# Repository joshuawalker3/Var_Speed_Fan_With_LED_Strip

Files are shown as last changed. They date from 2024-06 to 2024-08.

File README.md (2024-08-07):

# **Variable Speed Desk Fan with RGB LED for Use While Soldering**

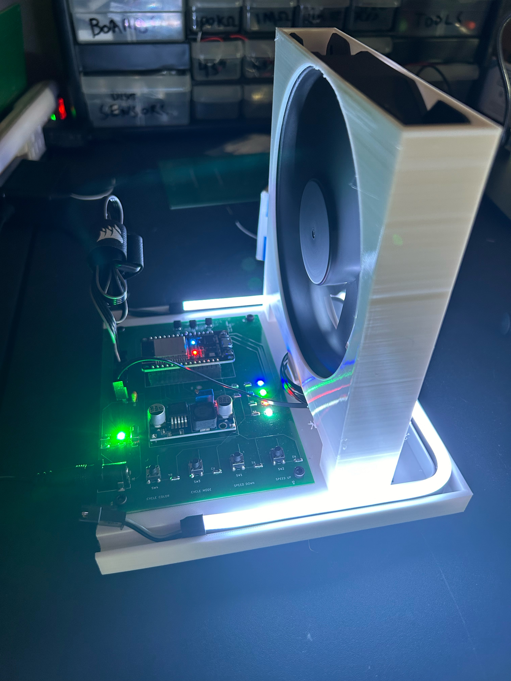
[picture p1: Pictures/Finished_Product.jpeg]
Final-Product


## **Project Overview**
An annoyance I’ve had while soldering is that the fumes from the flux burning off tends to drift directly in my face and up my nose. To solve this issue, I made this desktop fan. The fan is actually a PC chassis fan and the LED strip is a cheap LED strip. Any strip will work as long as they have a 4 pin connection and are Common Anode.

## **Code**
### *Overview*
The code is written in C. No IDE was used, only sublime text editor (because it’s the superior text editor).

Overall, the code is pretty straightforward. After initializing structs representing a motor (the fan) and the LED strip, they are used to initialize their respective functions then the drivers for each are started as their own task so they can run in “parallel”. The drivers and related functions are contained in components so the code header can be linked when the ELF is built by the toolchain.

The fan is represented in the code as a Pulse Width Modulated (PWM) DC-motor. The struct is used to set up the PWM module and the GPIO pins for controlling motor speed. A 2-bit resolution for the PWM was chosen since I only desired to have three speeds for the fan: off, half-power, and full-power. The motor driver polls the GPIO pins and, when an input is detected, changes the motor speed accordingly.

The LED strip is controlled via signals from 3 GPIO pins, 1 for each color. The LED has two modes. The static mode where a chosen color is displayed indefinitely and the cycle mode where every color combination is cycled through sequentially. The LED driver polls two input pins. The first input pin cycles through colors sequentially and can cycle power to the LED if pressed for 1 second. The second input changes the LED mode.
### *Challenges and Lessons Learned*
The biggest challenge with the code was figuring out the toolchain and how the build system works. A good chunk of time was spent trying to figure out how to integrate the header into the main code. The solution to this was obviously to RTFM. The biggest lesson learned was the value of structs. By putting all needed variables into pretty little structs, the code became easier to read as well as to write.

## **Chassis Design and Manufacture**
### *Overview*
The chassis was designed in FreeCAD, sliced using Ankermake default slicer, and printed on an Ankermake M5. It was printed as one solid piece. The chassis is simply a plastic base connected to a slot for the fan and slots for the LED strip and PCB. It was designed to be as compact as possible while maintaining stability.

#### FreeCAD Model
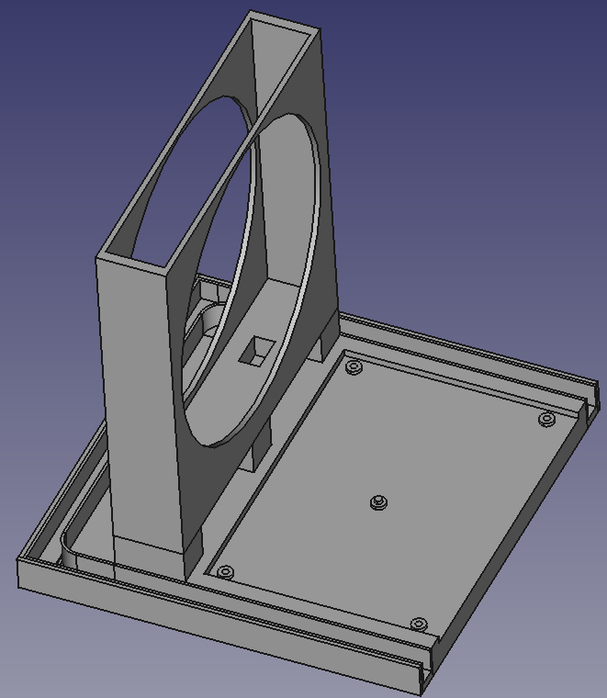
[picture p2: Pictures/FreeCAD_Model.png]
Model


### *Challenges and Lessons Learned*
The main challenge with the chassis was getting it to print properly. Since that are parts that are “floating” while the print is in process, supports were required for the fan slot and the circular vertical hole. The print failed twice for what is suspected to be the same reason. The solution was to simply to slow the speeds down across the board for the entire print. This caused the print time to inflate from around 11 hours to 30 hours.
#### Failed Print
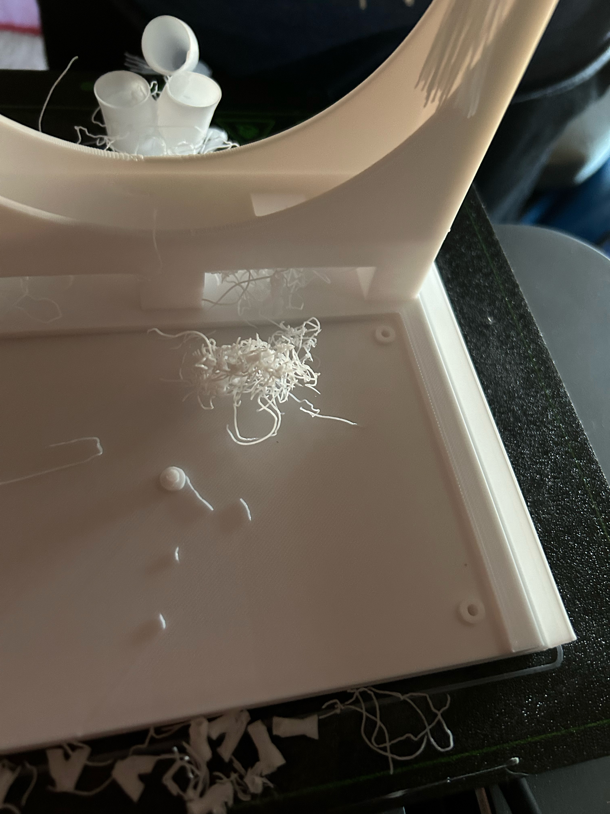
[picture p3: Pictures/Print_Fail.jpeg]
Print-Fail


#### Proper Print with Supports Connected
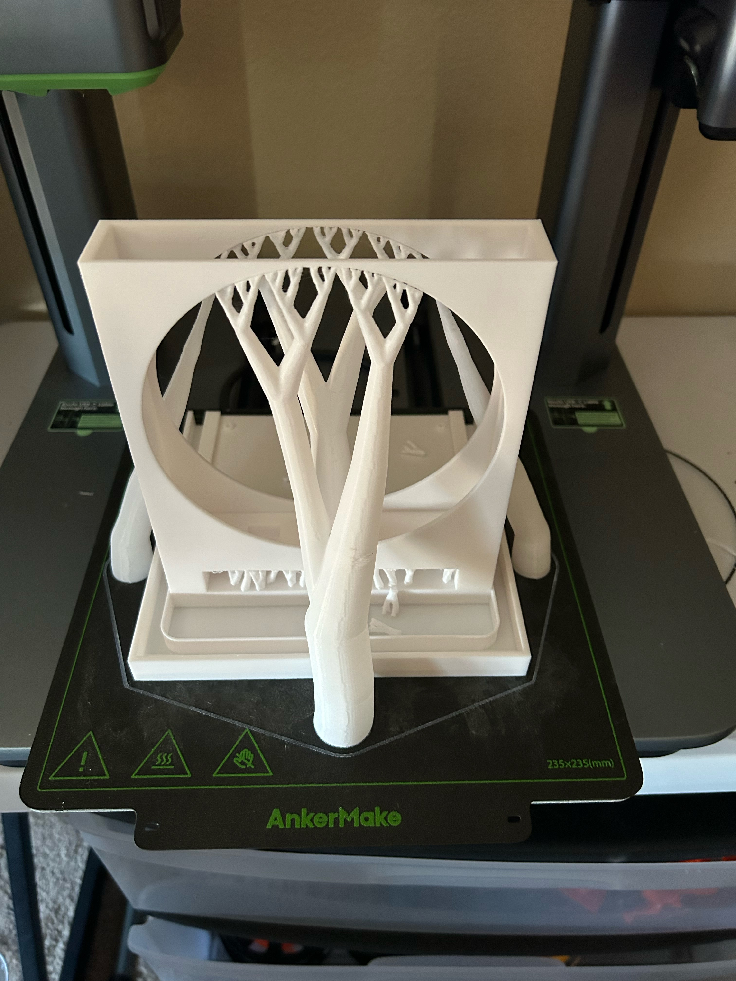
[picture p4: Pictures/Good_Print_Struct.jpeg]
Good-Print


#### Final Print
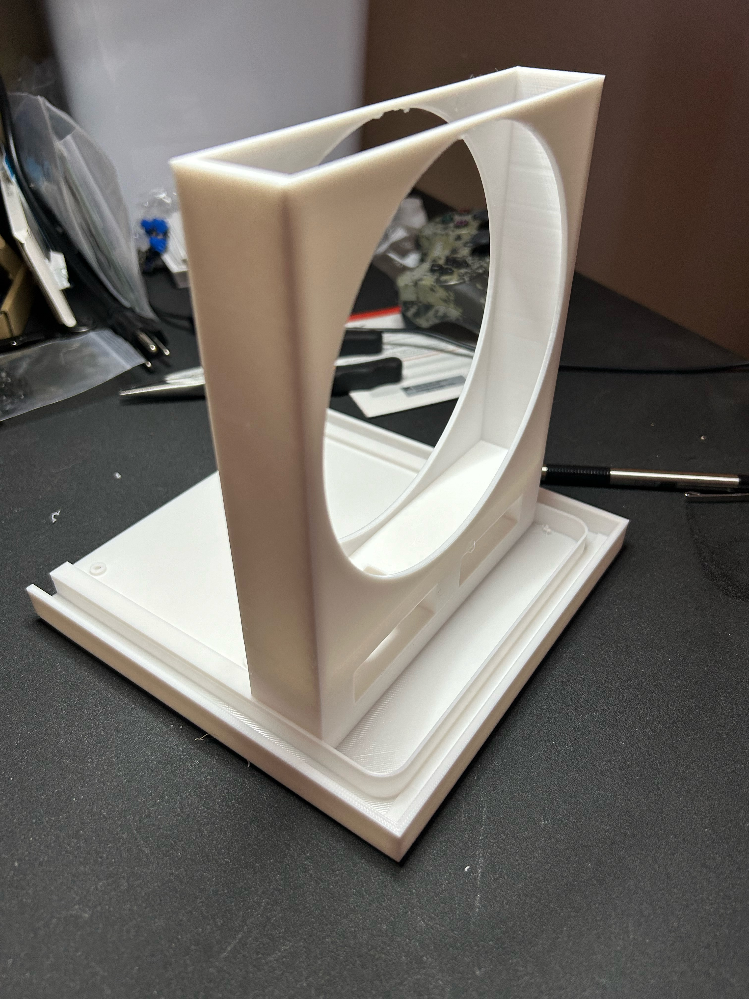
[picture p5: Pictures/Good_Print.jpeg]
Final-print


## **PCB Design**
### *Overview*
The PCB was designed using KiCAD and manufactured through PCBWay. I changed PCB manufacturers out of curiousity but could find no signifigance between PCBWay and Seeed Fusion.

Since the fan and LED strip require 12 VDC and the ESP32 requires between 3.3 – 6 VDC, the circuit is split by a buck converter that transforms 12VDC to8 around 5 VDC (I used 4.5 VDC). The PWM signal is sent directly from the ESP board to the fan. The LED strip interfaces to the ESP board via PN-2222A transistors.

#### PCB Schematic
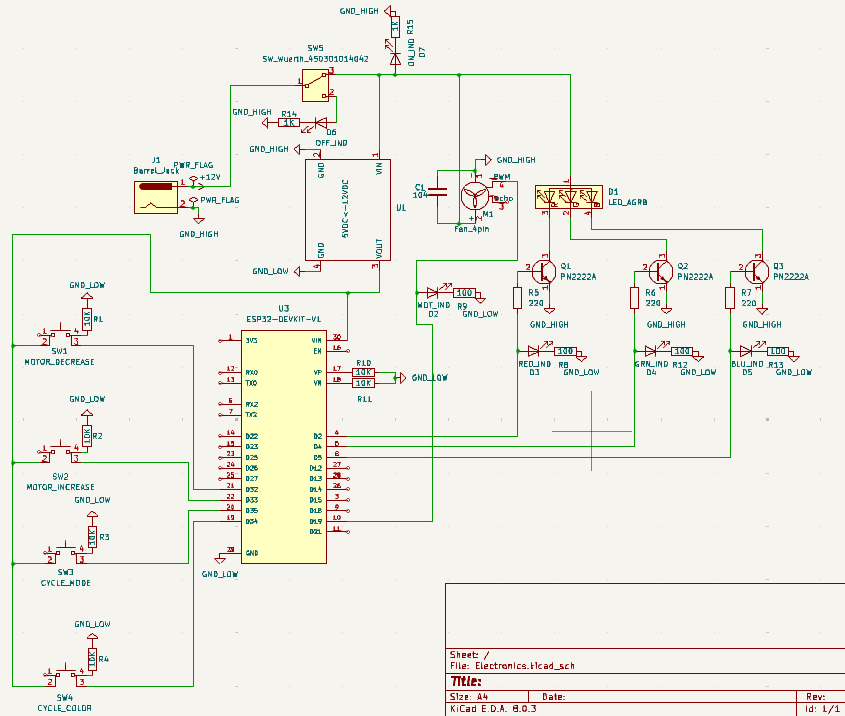
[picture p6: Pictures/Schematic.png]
Schematic


#### Circuit Prototype
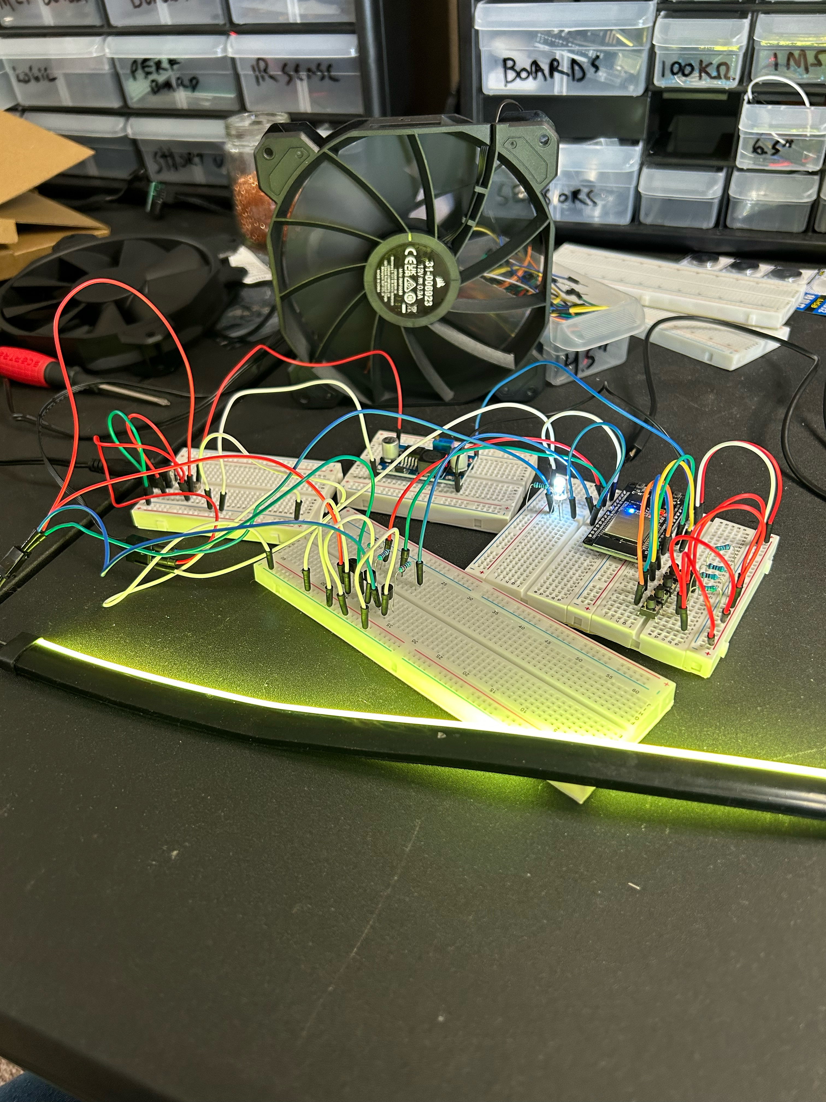
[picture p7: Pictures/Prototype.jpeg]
Prototype


#### PCB Design
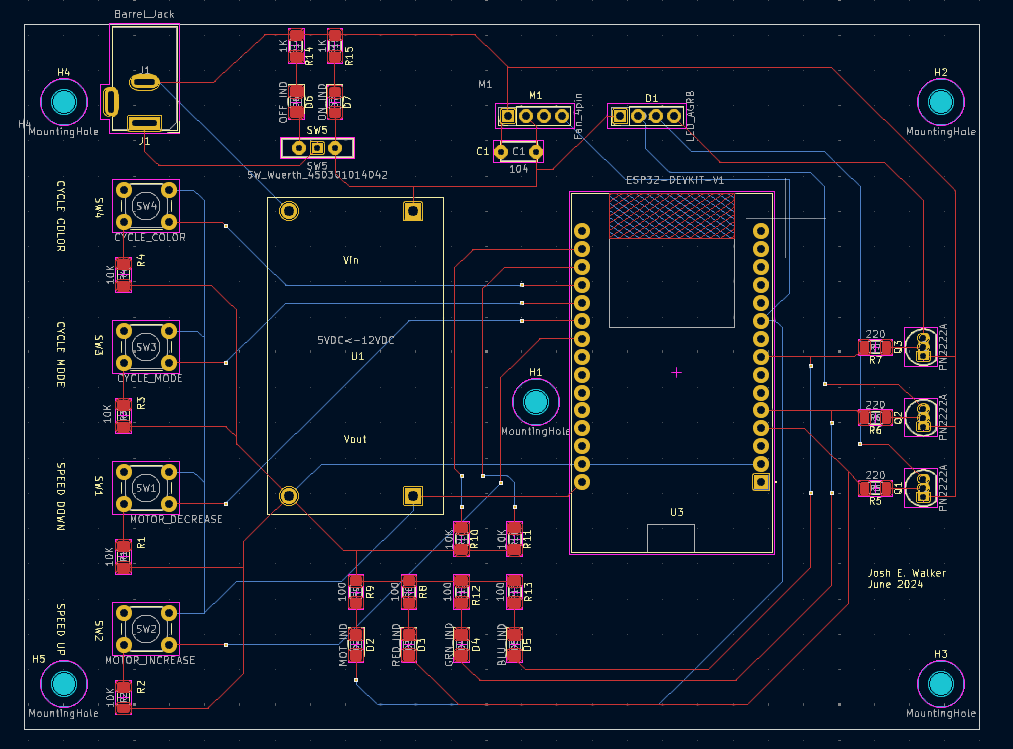
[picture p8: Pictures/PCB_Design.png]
PCB-Design


I also added some components to aid in troubleshooting such as LED’s that indicate that power is being applied to the board when off, an indication the model is on, LED’s connected in parallel to each LED GPIO to show proper response, and an LED in parallel to the fan that shows the status of the fan since the LED will change brightness as the PWM signal, and therefore fan speed, changes.
### *Challenges and Lessons Learned*
This was a big step for me in PCB design since it had more components than I had ever used before. This meant that I had to be creative with routing traces. To further remove trace clutter on the PCB, I added via’s so I could have traces on both the top and bottom of the PCB.

#### PCB Comparison Before and After Soldering Components
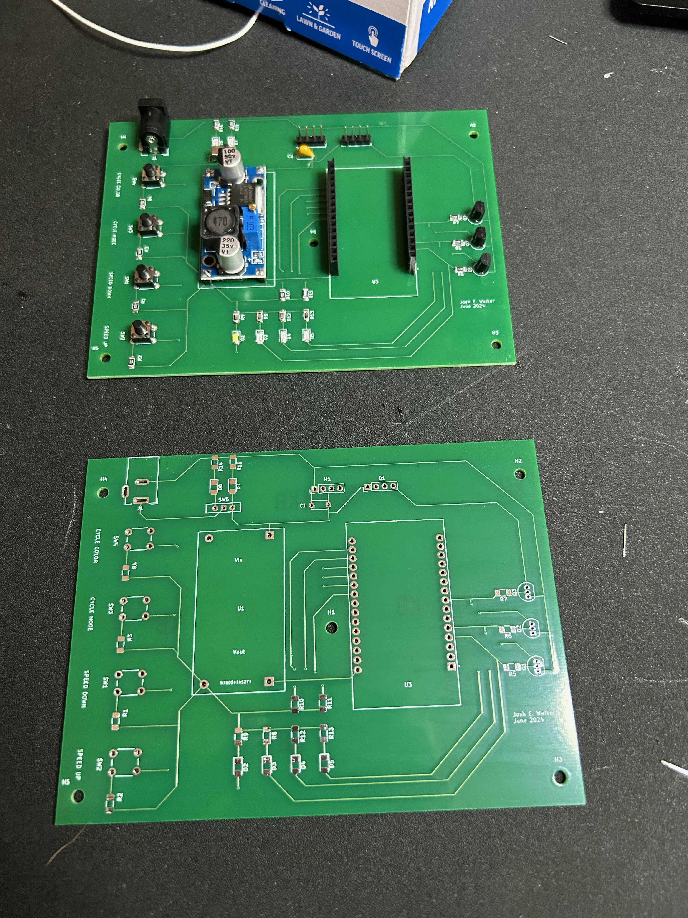
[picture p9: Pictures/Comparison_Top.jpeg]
Top

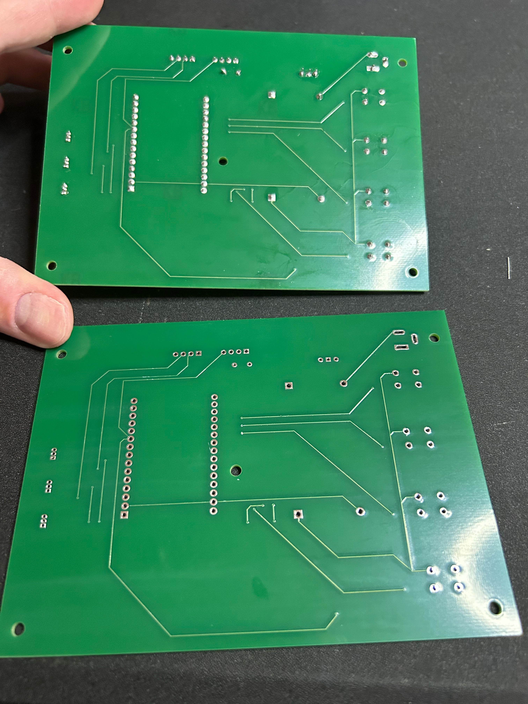
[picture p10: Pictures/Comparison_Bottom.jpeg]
Bottom


#### PCB Mounted on Chassis
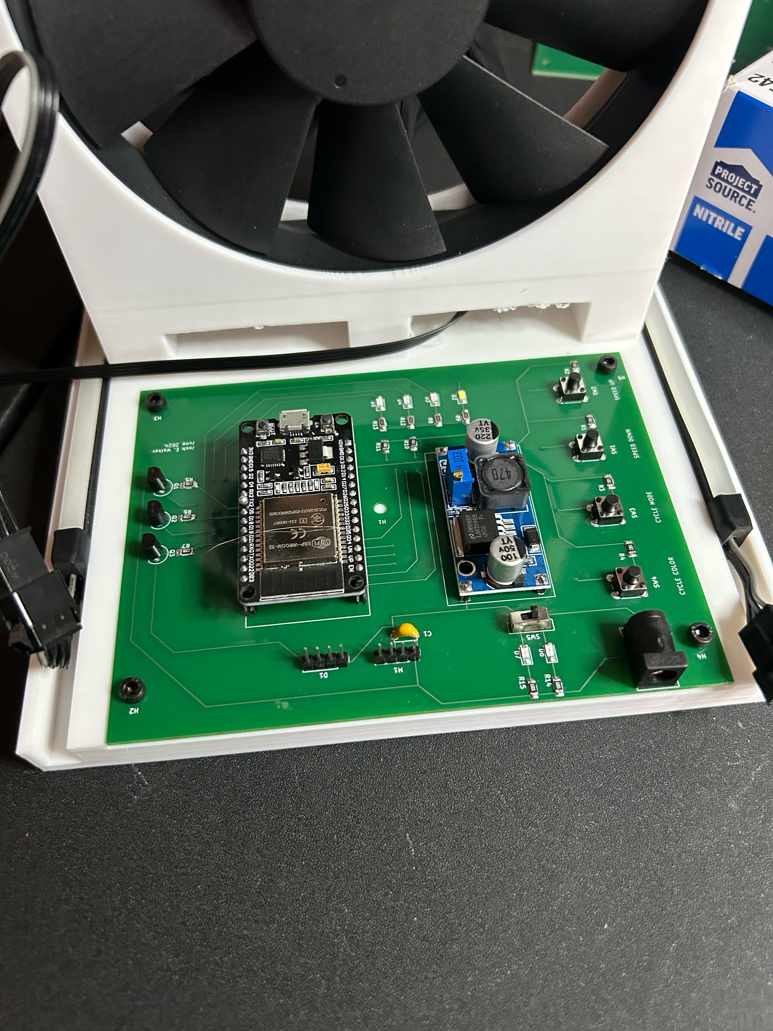
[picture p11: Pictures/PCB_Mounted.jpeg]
Mounted


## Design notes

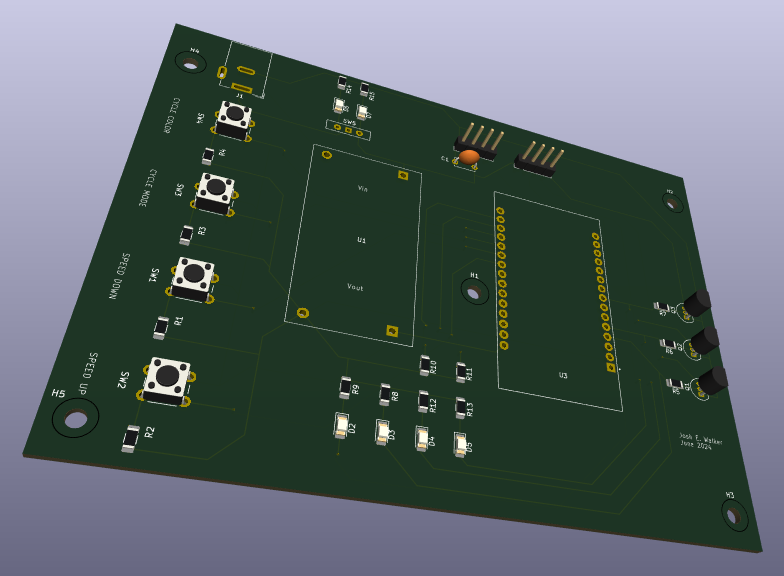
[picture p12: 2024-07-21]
Pictures/3D_PCB_View.png

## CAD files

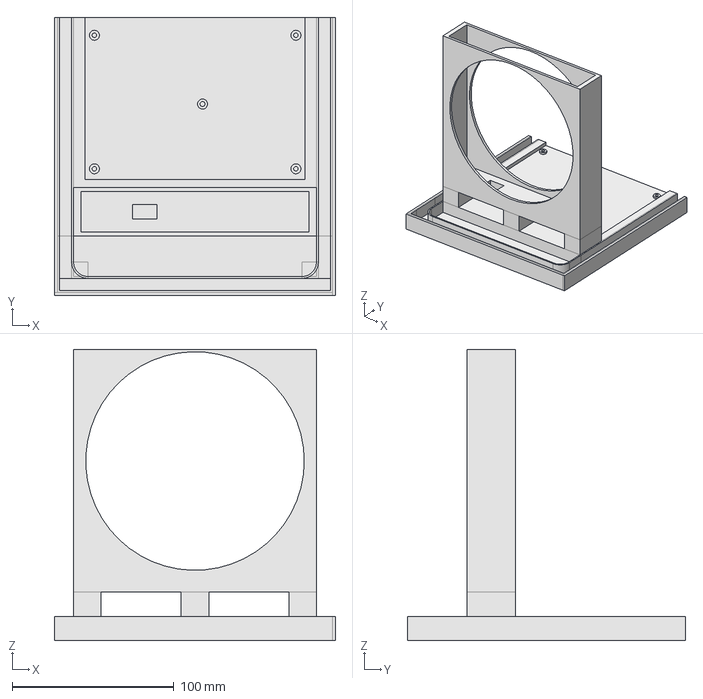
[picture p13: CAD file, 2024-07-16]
Object-Model/Fan-Case.FCStd
173.6 x 171.8 x 180.0 mm

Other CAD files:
Object-Model/Fan-Case-Body.stl
Object-Model/Fan-Case.stl

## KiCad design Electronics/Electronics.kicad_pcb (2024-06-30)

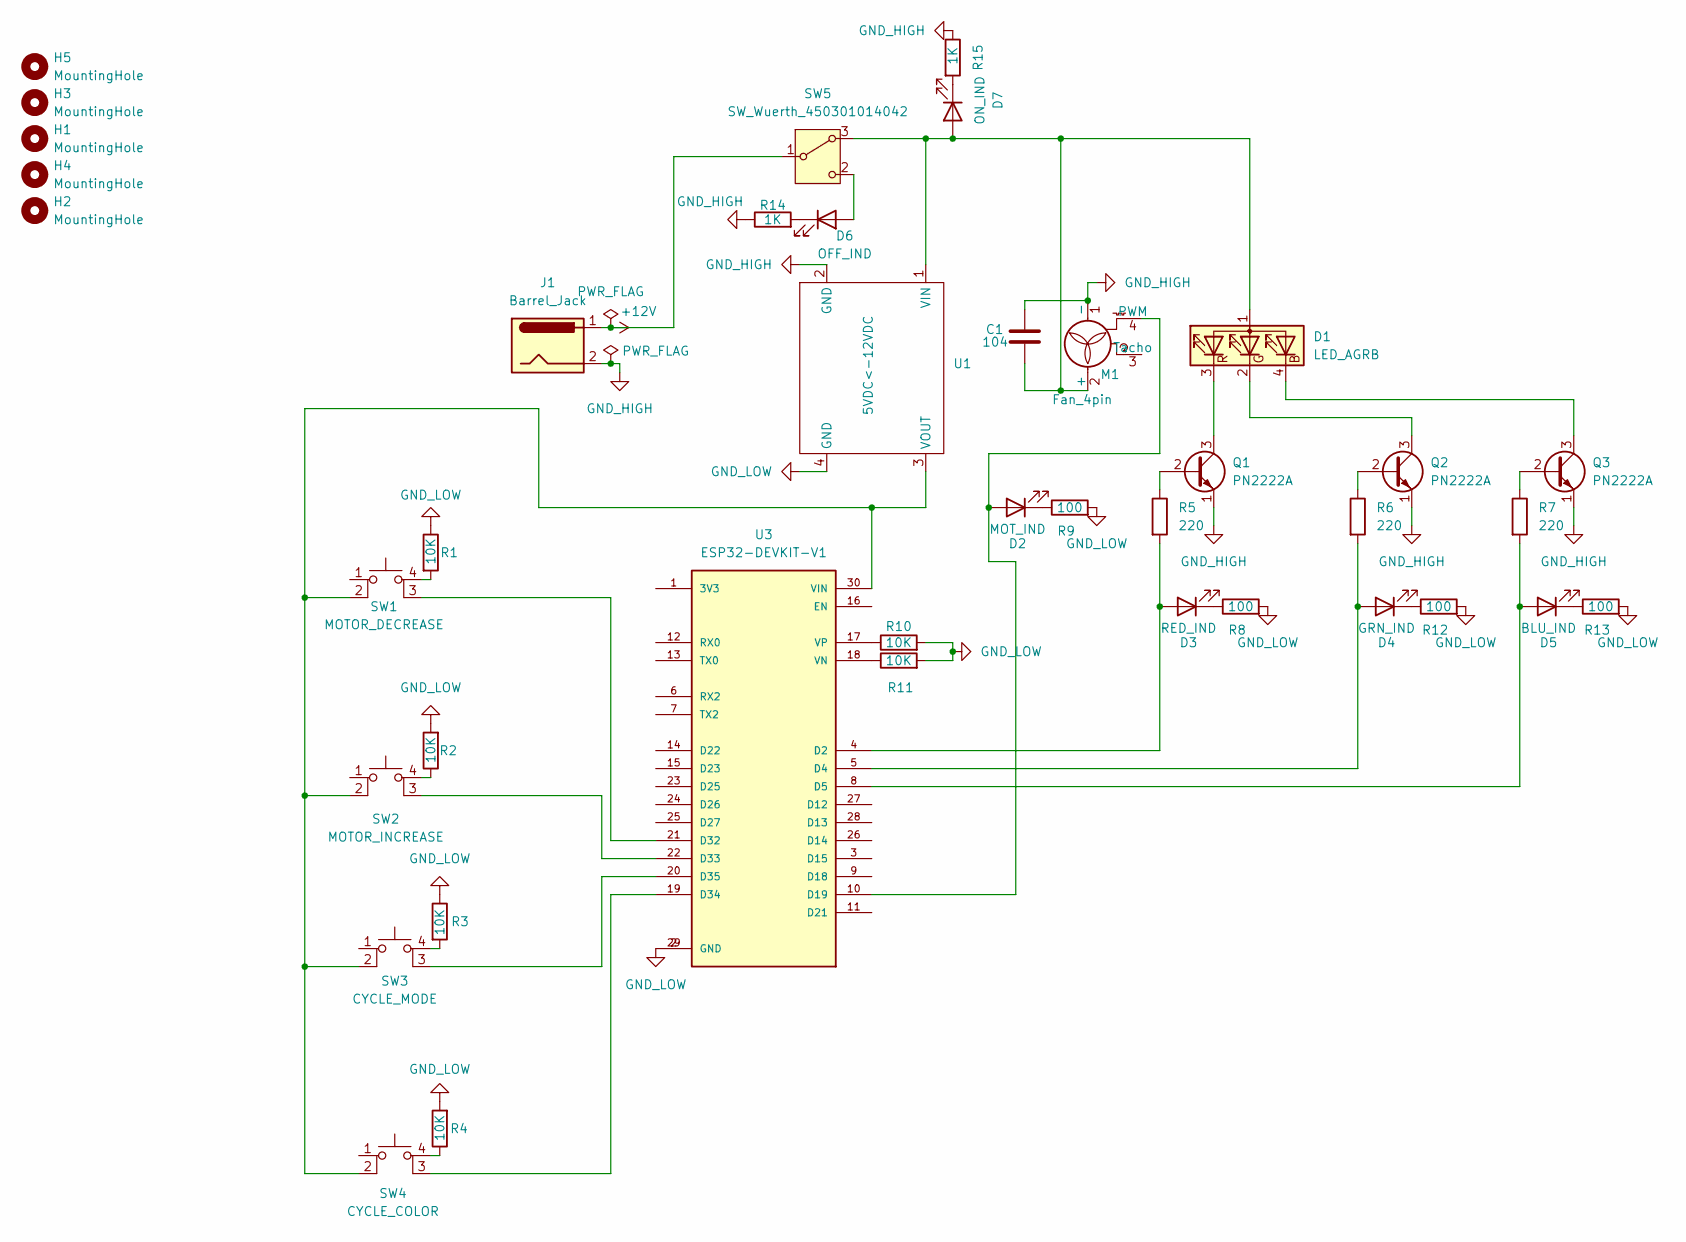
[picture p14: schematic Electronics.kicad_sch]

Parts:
C1: 104; C_Disc_D5.0mm_W2.5mm_P5.00mm
D1: LED_AGRB; PinHeader_1x04_P2.54mm_Vertical
D2: MOT_IND; LED_1206_3216Metric_Pad1.42x1.75mm_HandSolder
D3: RED_IND; LED_1206_3216Metric_Pad1.42x1.75mm_HandSolder
D4: GRN_IND; LED_1206_3216Metric_Pad1.42x1.75mm_HandSolder
D5: BLU_IND; LED_1206_3216Metric_Pad1.42x1.75mm_HandSolder
D6: OFF_IND; LED_1206_3216Metric_Pad1.42x1.75mm_HandSolder
D7: ON_IND; LED_1206_3216Metric_Pad1.42x1.75mm_HandSolder
H1, H2, H3, H4, H5: MountingHole; MountingHole_3.2mm_M3
J1: Barrel_Jack; BarrelJack_Wuerth_6941xx301002
M1: Fan_4pin; PinHeader_1x04_P2.54mm_Vertical
Q1, Q2, Q3: PN2222A; TO-92_Inline
R1, R2, R3, R4, R10, R11: 10K; R_1206_3216Metric_Pad1.30x1.75mm_HandSolder
R5, R6, R7: 220; R_1206_3216Metric_Pad1.30x1.75mm_HandSolder
R8, R9, R12, R13: 100; R_1206_3216Metric_Pad1.30x1.75mm_HandSolder
R14, R15: 1K; R_1206_3216Metric_Pad1.30x1.75mm_HandSolder
SW1: MOTOR_DECREASE; SW_PUSH_6mm
SW2: MOTOR_INCREASE; SW_PUSH_6mm
SW3: CYCLE_MODE; SW_PUSH_6mm
SW4: CYCLE_COLOR; SW_PUSH_6mm
SW5: SW_Wuerth_450301014042; SW_Slide-03_Wuerth-WS-SLTV_10x2.5x6.4_P2.54mm
U1: 5VDC<-12VDC; Buck_Converter
U3: ESP32-DEVKIT-V1; MODULE_ESP32_DEVKIT_V1_NO_MOUNT; PARTREV N/A

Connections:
+12V: J1.1, SW5.1 (B)
GND_HIGH: C1.1, J1.2, M1.1 (-), Q1.1 (E), Q2.1 (E), Q3.1 (E), R14.1, R15.1, U1.2 (GND)
GND_LOW: R1.1, R2.2, R3.1, R4.2, R8.2, R9.2, R10.2, R11.2, R12.2, R13.2, U1.4 (GND), U3.2 (GND), U3.29 (GND)
unnamed: C1.2, D1.1 (A), D7.2 (A), M1.2 (+), SW5.3 (A), U1.1 (VIN)
unnamed: D1.4 (BK), Q3.3 (C)
unnamed: D1.2 (GK), Q2.3 (C)
unnamed: D1.3 (RK), Q1.3 (C)
unnamed: D2.2 (A), M1.4 (PWM), U3.10 (D19)
unnamed: D2.1 (K), R9.1
unnamed: D3.2 (A), R5.2, U3.4 (D2)
unnamed: D3.1 (K), R8.1
unnamed: D4.2 (A), R6.2, U3.5 (D4)
unnamed: D4.1 (K), R12.1
unnamed: D5.2 (A), R7.2, U3.8 (D5)
unnamed: D5.1 (K), R13.1
unnamed: D6.2 (A), SW5.2 (C)
unnamed: D6.1 (K), R14.2
unnamed: D7.1 (K), R15.2
unnamed: Q1.2 (B), R5.1
unnamed: Q2.2 (B), R6.1
unnamed: Q3.2 (B), R7.1
unnamed: R1.2, SW1.4 (A)
unnamed: SW1.3 (K), U3.21 (D32)
unnamed: R2.1, SW2.4 (A)
unnamed: SW2.3 (K), U3.22 (D33)
unnamed: R3.2, SW3.4 (A)
unnamed: SW3.3 (K), U3.20 (D35)
unnamed: R4.1, SW4.4 (A)
unnamed: SW4.3 (K), U3.19 (D34)
unnamed: SW1.2, SW2.2, SW3.2, SW4.2, U1.3 (VOUT), U3.30 (VIN)
unnamed: R11.1, U3.18 (VN)
unnamed: R10.1, U3.17 (VP)

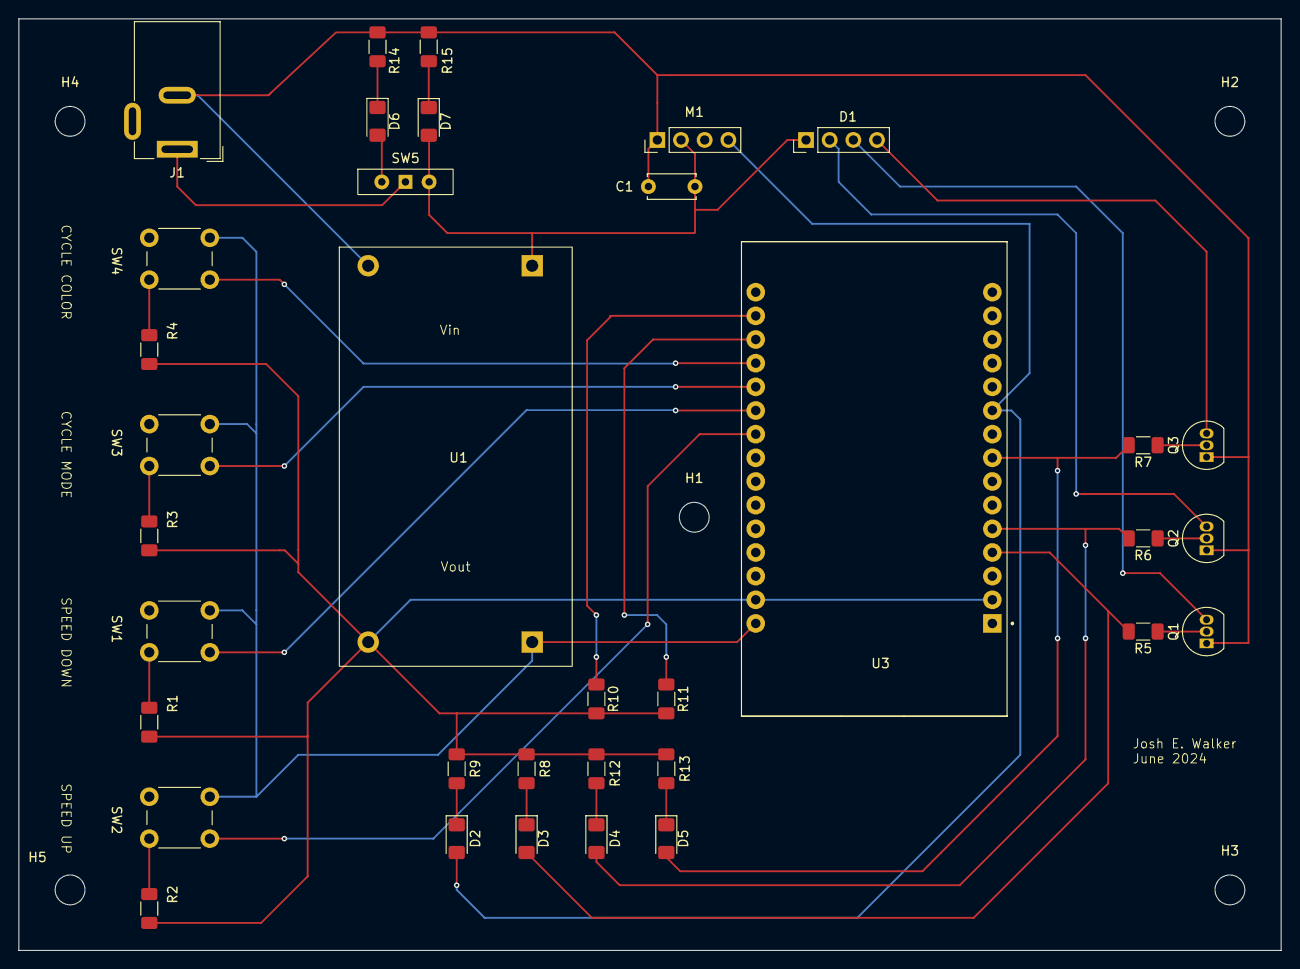
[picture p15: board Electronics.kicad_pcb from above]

Board: 2 copper layers, 135.5 x 100.0 mm, 40 parts (0 on the bottom side), 32 nets.

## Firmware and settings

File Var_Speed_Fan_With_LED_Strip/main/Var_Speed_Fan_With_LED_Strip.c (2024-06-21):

/*
Author: Joshua Walker
Date: 19-June-2024
Version: 1.0

Var_Speed_Fan_With_LED_Strip.c initializes an ESP32 DEVKIT Board
for use with 1 12V Brushless DC Fan (reffered to as motor) and 
1 12V RGB LED Strip (referred to as LED_Strip).
Upon completion of initialization, the drivers for both components
are started and app_main returns.

The final .elf was built using ESP-IDF v5.3-dev with a set target of ESP32.
*/

#include <stdio.h>
#include "freertos/FreeRTOS.h"
#include "freertos/task.h"
#include "led_ctrl.h"
#include "motor_ctrl_2_bit.h"

/*
Constants for motor. 
*/
#define MOTOR_TIMER LEDC_TIMER_0 //1 of 4 timers
#define MOTOR_MODE LEDC_LOW_SPEED_MODE //Changes to speed done by function call
#define MOTOR_CHANNEL LEDC_CHANNEL_0 //1 of 8 channels
#define MOTOR_CLK_CFG LEDC_AUTO_CLK //Default clk ctrl
#define MOTOR_INTR_TYPE LEDC_INTR_DISABLE //Disable interrupts
#define MOTOR_FREQUENCY 4000 //4 kHz
#define MOTOR_PHASE_SHIFT 0 //0 phase shift
#define MOTOR_PWM_PIN 19 //Motor PWM Pin
#define MOTOR_DECREASE_PIN 32 //Decrease speed button
#define MOTOR_INCREASE_PIN 33 //Increase speed button

/*
Constants for LED Strip
*/
#define LED_RED_PIN 2
#define LED_GREEN_PIN 4
#define LED_BLUE_PIN 5
#define LED_CYCLE_COLOR_PIN 34
#define LED_CYCLE_MODE_PIN 35

#define STACK_STD 2048 //std stack size for drivers

Motor_Struct_2_Bit motor = {
	.timer = MOTOR_TIMER,
	.mode = MOTOR_MODE,
	.channel = MOTOR_CHANNEL,
	.clk_cfg = MOTOR_CLK_CFG,
	.intr_type = MOTOR_INTR_TYPE,
	.freq_hz = MOTOR_FREQUENCY,
	.hpoint = MOTOR_PHASE_SHIFT,
	.pwm_pin = MOTOR_PWM_PIN,
	.decrease_pin = MOTOR_DECREASE_PIN,
	.increase_pin = MOTOR_INCREASE_PIN,
	.motor_power = ZERO_POWER
};

LED_Struct LED_Strip = {
	.red_pin = LED_RED_PIN,
	.green_pin = LED_GREEN_PIN,
	.blue_pin = LED_BLUE_PIN,
	.cycle_color_button = LED_CYCLE_COLOR_PIN,
	.cycle_mode_button = LED_CYCLE_MODE_PIN,
	.light_combo = RED,
	.curr_mode = STATIC
};

void app_main(void) {
	led_strip_init(&LED_Strip);

	motor_init(&motor);

	xTaskCreate(motor_driver, "Motor Driver", STACK_STD, (void*)&motor, 2, NULL);
	
	xTaskCreate(led_driver, "LED Strip Driver", STACK_STD, (void*)&LED_Strip, 2, NULL);
}

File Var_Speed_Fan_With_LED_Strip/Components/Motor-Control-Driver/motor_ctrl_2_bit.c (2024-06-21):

/*
Author: Joshua Walker
Date: 18-June-2024
Version: 1.0
*/

#include "freertos/FreeRTOS.h"
#include "esp_err.h"
#include "esp_log.h"
#include "driver/ledc.h" //Chosen for simplicity
#include "driver/gpio.h"
#include "motor_ctrl_2_bit.h"

/*
init_timer initializes the timer for the PWM module
args: motor a pointer to a struct representing a PWM DC Motor
*/
void init_timer(Motor_Struct_2_Bit* motor) {
	char* taskName = pcTaskGetName(NULL);

	ESP_LOGI(taskName, "Initializing Motor Timer....");

	ledc_timer_config_t ledc_timer = {
		.speed_mode = motor->mode, 
		.duty_resolution = LEDC_TIMER_2_BIT, //Duty resolution of 2 bits (2**2 discrete values range [0, 4]) 
		.timer_num = motor->timer, 
		.freq_hz = motor->freq_hz, 
		.clk_cfg = motor->clk_cfg 
	};

	ESP_ERROR_CHECK(ledc_timer_config(&ledc_timer));
}

/*
init_channel initializes the channel for the PWM module
args: motor a pointer to a struct representing a PWM DC Motor
*/
void init_channel(Motor_Struct_2_Bit* motor) {
	char* taskName = pcTaskGetName(NULL);

	ESP_LOGI(taskName, "Initializing Motor Channel....");
	
	ledc_channel_config_t ledc_channel = {
		.speed_mode = motor->mode, 
		.channel = motor->channel, 
		.timer_sel = motor->timer, 
		.intr_type = motor->intr_type, 
		.gpio_num = motor->pwm_pin, 
		.duty = motor->motor_power, 
		.hpoint = motor->hpoint //set phase shift. Typically 0
	};

	ESP_ERROR_CHECK(ledc_channel_config(&ledc_channel));
}

/*
update_and_change_motor_speed sets the duty resolution (speed) for a channel then
updates the cchannel
args: motor a pointer to a struct representing a PWM DC Motor
*/
void update_and_change_motor_speed(Motor_Struct_2_Bit* motor) {
	char* taskName = pcTaskGetName(NULL);

	ESP_LOGI(taskName, "Changing Motor Speed!");
	
	ESP_ERROR_CHECK(ledc_set_duty(motor->mode, motor->channel, motor->motor_power)); 

	ESP_ERROR_CHECK(ledc_update_duty(motor->mode, motor->channel));
}

/*
init_motor_speed_buttons initializes the input GPIO pins for changing
motor speed 
args: motor a pointer to a struct representing a PWM DC Motor
*/
void init_motor_speed_buttons(Motor_Struct_2_Bit* motor) {
	char* taskName = pcTaskGetName(NULL);

	ESP_LOGI(taskName, "Initializing Motor Speed Change Buttons....");
	
	//reset pin buffers
	ESP_ERROR_CHECK(gpio_reset_pin(motor->increase_pin));
	ESP_ERROR_CHECK(gpio_reset_pin(motor->decrease_pin));

	//Start Pins
	ESP_ERROR_CHECK(gpio_set_direction(motor->increase_pin, GPIO_MODE_INPUT));
	ESP_ERROR_CHECK(gpio_set_direction(motor->decrease_pin, GPIO_MODE_INPUT));
}

/*
motor_init initializes a dev board for use with a PWM DC Motor
args: motor a pointer to a struct representing a PWM DC Motor
*/
void motor_init(Motor_Struct_2_Bit* motor) {
	char* taskName = pcTaskGetName(NULL);

	ESP_LOGI(taskName, "Initializing Motor....");
	
	init_timer(motor);

	init_channel(motor);

	init_motor_speed_buttons(motor);

	ESP_LOGI(taskName, "Completed Initializing Motor....");
}

/*
motor_driver is the main driver for controlling a PWM motor.
args: args a void pointer passed in when the task is created.
*/
void motor_driver(void* args) {
	char* taskName = pcTaskGetName(NULL);

	ESP_LOGI(taskName, "Motor Driver started....");

	Motor_Struct_2_Bit* motor = (Motor_Struct_2_Bit*)args;
	
	update_and_change_motor_speed(motor);

	while(1) {
		if (!gpio_get_level(motor->decrease_pin) != !gpio_get_level(motor->increase_pin)) { //XOR Operation. Prevents acting on simultaneous button presses
			if (gpio_get_level(motor->decrease_pin) && motor->motor_power != ZERO_POWER) {
				ESP_LOGI(taskName, "Decreasing Motor Power. Slowin her down Boss!");

				motor->motor_power -= 2;

				update_and_change_motor_speed(motor);

				while (gpio_get_level(motor->decrease_pin)) {
					delay(10);
				}
			}
			if (gpio_get_level(motor->increase_pin) && motor->motor_power != HIGH_POWER) {
				ESP_LOGI(taskName, "Increasing Motor Power. YeeHaw!");

				motor->motor_power += 2;
				
				update_and_change_motor_speed(motor);

				while (gpio_get_level(motor->increase_pin)) {
					delay(10);
				}
			}
		}
		delay(10);
	}
}

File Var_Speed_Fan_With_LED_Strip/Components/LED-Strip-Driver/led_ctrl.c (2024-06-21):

/*
Author: Joshua Walker
Date: 18-June-2024
Version: 1.0
*/

#include "freertos/FreeRTOS.h"
#include "freertos/task.h"
#include "driver/gpio.h"
#include "esp_err.h"
#include "esp_log.h"
#include "led_ctrl.h"


/**
led_strip_led_init initializes the output GPIO pinsfor an RGB LED Strip
args: LED_Strip a pointer to a struct representing a RGB LED Strip
*/
void led_strip_led_init(LED_Struct* LED_Strip) {
	char* taskName = pcTaskGetName(NULL);

	ESP_LOGI(taskName, "Initializing LED Pins...");

	//reset pin buffers
	ESP_ERROR_CHECK(gpio_reset_pin(LED_Strip->red_pin));
	ESP_ERROR_CHECK(gpio_reset_pin(LED_Strip->green_pin));
	ESP_ERROR_CHECK(gpio_reset_pin(LED_Strip->blue_pin));

	//Start Pins
	ESP_ERROR_CHECK(gpio_set_direction(LED_Strip->red_pin, GPIO_MODE_OUTPUT));
	ESP_ERROR_CHECK(gpio_set_direction(LED_Strip->green_pin, GPIO_MODE_OUTPUT));
	ESP_ERROR_CHECK(gpio_set_direction(LED_Strip->blue_pin, GPIO_MODE_OUTPUT));
}

/*
color_button_init initizlizes the input for the input GPIO pin connected
to a tactile switch to allow for switching colors in STATIC mode
args: LED_Strip a pointer to a struct representing a RGB LED Strip
*/
void color_button_init(LED_Struct* LED_Strip) {
	char* taskName = pcTaskGetName(NULL);

	ESP_LOGI(taskName, "Initializing LED Color Change Button...");

	//reset pin buffers
	ESP_ERROR_CHECK(gpio_reset_pin(LED_Strip->cycle_color_button));

	//Start Pins
	ESP_ERROR_CHECK(gpio_set_direction(LED_Strip->cycle_color_button, GPIO_MODE_INPUT));
}

/*
mode_button_init initizlizes the input for the input GPIO pin connected
to a tactile switch to allow for switching of modes
args: LED_Strip a pointer to a struct representing a RGB LED Strip
*/
void mode_button_init(LED_Struct* LED_Strip) {
	char* taskName = pcTaskGetName(NULL);

	ESP_LOGI(taskName, "Initializing LED Mode Change Button...");

	//reset pin buffers
	ESP_ERROR_CHECK(gpio_reset_pin(LED_Strip->cycle_mode_button));

	//Start Pins
	ESP_ERROR_CHECK(gpio_set_direction(LED_Strip->cycle_mode_button, GPIO_MODE_INPUT));
}

/*
led_strip_init initializes a the dev board for use with an RGB LED strip
args: LED_Strip a pointer to a struct representing a RGB LED Strip
*/
void led_strip_init(LED_Struct* LED_Strip) {
	char* taskName = pcTaskGetName(NULL);

	ESP_LOGI(taskName, "Initializing LED Strip...");

	led_strip_led_init(LED_Strip);

	color_button_init(LED_Strip);

	mode_button_init(LED_Strip);

	ESP_LOGI(taskName, "Completed Initializing LED Strip...");
}

/*
led_strip_static_color is the driver for when the mode is STATIC
args: args a void pointer passed in when the task is created
*/
void led_strip_static_color(void* args) {
	char* taskName = pcTaskGetName(NULL);

	ESP_LOGI(taskName, "LED STATIC Color Task Started!");

	LED_Struct* LED_Strip = (LED_Struct*)args;

	set_led_color_switch(LED_Strip);

	while (1) {
		if (gpio_get_level(LED_Strip->cycle_color_button)) {
			int counter = 0; //Counter to determine mhow long button has been pressed in increments of hundredths of a second 

			while (gpio_get_level(LED_Strip->cycle_color_button)) {
				counter++;
				delay(10);
			}

			if (counter >= 100) {
				LED_Strip->light_combo = ALL_OFF;
			}
			else if (LED_Strip->light_combo == ALL_ON) {
				LED_Strip->light_combo = RED;
			}
			else {
				LED_Strip->light_combo++;
			}

			set_led_color_switch(LED_Strip);
		}
		delay(10);
	}
}

/*
led_strip_cycle_color is the driver for when the mode is CYCLE
args: args a void pointer passed in when the task is created
*/
void led_strip_cycle_colors(void* args) {
	char* taskName = pcTaskGetName(NULL);

	ESP_LOGI(taskName, "LED CYCLE Color Task Started!");

	LED_Struct* LED_Strip = (LED_Struct*)args;

	if (LED_Strip->light_combo == ALL_OFF) {
		LED_Strip->light_combo = ALL_ON - 1; 
	}

	while (1) {
		if (LED_Strip->light_combo == ALL_ON) {
			LED_Strip->light_combo = RED;
		}
		else {
			LED_Strip->light_combo++;
		}

		set_led_color_switch(LED_Strip);
		
		delay(1000);
	}
}

/*
led_driver is the main driver for the LED strip. It switches tasks whenever the mode change
signal is received.
args: args a void pointer passed in when the task is created. Typically NULL
*/
void led_driver(void* args) {
	char* taskName = pcTaskGetName(NULL);

	ESP_LOGI(taskName, "LED Driver started....");

	LED_Struct* LED_Strip = (LED_Struct*)args;
	
	if (LED_Strip->curr_mode == STATIC) {
		xTaskCreate(led_strip_static_color, "LED Static Mode", 2048, (void*)LED_Strip, 2, &(LED_Strip->Static_Mode_Handle));

		ESP_LOGI(taskName, "Initial LED Mode STATIC!");
	}
	else {
		xTaskCreate(led_strip_cycle_colors, "LED Cycle Mode", 2048, (void*)LED_Strip, 2, &(LED_Strip->Cycle_Mode_Handle));

		ESP_LOGI(taskName, "Initial LED Mode CYCLE!");
	}
	
	while (1) {
		if (gpio_get_level(LED_Strip->cycle_mode_button)) {
			LED_Strip->curr_mode = -(LED_Strip->curr_mode);

			if (LED_Strip->curr_mode == STATIC) {
				vTaskDelete(LED_Strip->Cycle_Mode_Handle);
				LED_Strip->Cycle_Mode_Handle = NULL;

				xTaskCreate(led_strip_static_color, "LED Static Mode", 2048, (void*)LED_Strip, 2, &(LED_Strip->Static_Mode_Handle));

				ESP_LOGI(taskName, "LED Mode changed to STATIC!");
			}
			else {
				vTaskDelete(LED_Strip->Static_Mode_Handle);
				LED_Strip->Static_Mode_Handle = NULL;

				xTaskCreate(led_strip_cycle_colors, "LED Cycle Mode", 2048, (void*)LED_Strip, 2, &(LED_Strip->Cycle_Mode_Handle));

				ESP_LOGI(taskName, "LED Mode changed to CYCLE!");
			}

			while (gpio_get_level(LED_Strip->cycle_mode_button)) {
				delay(10);
			}
		}
		delay(10);
	}
}

/*
set_led_color_switch is a switch for determining what LEDs in the LED strip
need to be illuminated based upon current light combo.
args: LED_Strip a pointer to a struct representing a RGB LED Strip
*/
void set_led_color_switch(LED_Struct* LED_Strip) {
	char* taskName = pcTaskGetName(NULL);

	switch (LED_Strip->light_combo) {
		case ALL_OFF:
			set_led_color(LED_Strip, OFF, OFF, OFF);

			ESP_LOGI(taskName, "All LEDs Off!");

			break;
		case RED:
			set_led_color(LED_Strip, ON, OFF, OFF);

			ESP_LOGI(taskName, "Red LED On!");

			break;
		case GREEN:
			set_led_color(LED_Strip, OFF, ON, OFF);

			ESP_LOGI(taskName, "Green LED On!");

			break;
		case BLUE:
			set_led_color(LED_Strip, OFF, OFF, ON);

			ESP_LOGI(taskName, "Blue LED On!");

			break;
		case RED_GREEN:
			set_led_color(LED_Strip, ON, ON, OFF);

			ESP_LOGI(taskName, "Red And Green LEDs On!");

			break;
		case RED_BLUE:
			set_led_color(LED_Strip, ON, OFF, ON);

			ESP_LOGI(taskName, "Red And Blue LEDs On!");

			break;
		case GREEN_BLUE:
			set_led_color(LED_Strip, OFF, ON, ON);

			ESP_LOGI(taskName, "Green And Blue LEDs On!");

			break;
		case ALL_ON:
			set_led_color(LED_Strip, ON, ON, ON);

			ESP_LOGI(taskName, "All LEDs On! It sure is bright!");
			
			break;
		default:
			break;
	}
}
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

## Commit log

2024-06-19 Need to finish motor component
2024-06-21 Finished prototype. Next Step: Design Case!
2024-06-23 Added schematic
    [Electronics.kicad_pcb, Electronics.kicad_sch]
2024-06-25 Updated schematic. Working on footprints. Need to add new DevKit Symbol to schematic
    [Electronics.kicad_sch]
2024-06-26 Began PCB design. Updated Footprints. Added Indication LEDs
    [Electronics.kicad_pcb, Electronics.kicad_sch]
2024-06-30 Finalized. Awaiting PCB Production
    [Electronics-B_Cu.gbr, Electronics-B_Mask.gbr, Electronics-B_Paste.gbr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]
2024-07-08 Making progress on chassis. Need RGB Strip holder design
    [Fan-Case-Body.stl, Fan-Case.FCStd]
2024-07-08 Completed Chassis Version 1. Awaiting print
    [Fan-Case.FCStd]
2024-07-08 Modified fan pocket. First print failed (supports issue). Reprint
    [Fan-Case-Body.stl, Fan-Case.FCStd, Fan-Case.stl]
2024-07-16 Final Design
    [Fan-Case-Body.stl, Fan-Case.FCStd]
